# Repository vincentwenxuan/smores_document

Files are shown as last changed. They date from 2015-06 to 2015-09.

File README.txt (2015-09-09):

This file focus on the auto-calibration method. To make the codes work, we added and changed some commands in the main functions, both in atmega and stm32.
Some head files and c/cpp files also changed or added.

1. common_macros.h are added to store some macros which was defined in main functions. So pay attention about the multi-definition before merging.

2. TWI_slave.h is changed to prevent multi-definition.

3. Wiper_encoder.c is changed to make sure we can request the raw data without position/velocity calculation.

4. atm_cali.c and .h are added to do the auto calibraion in atmega part. You can just add one command in main code: cali_mode();   The atm_cali.c will do the rest part.

5. stm_cali.cpp and .h are added to do the the auto calibration in stm32 part. You can just add one command in main code: cali_cmd(left_wheel_motor, right_wheel_motor, right_pan_tilt_motor, left_pan_tilt_motor); The stm_cali.cpp will do the rest part.

6. USART.c and .h are deleted to prevent the memory overflow in atmega. Remember to put them back when new chips are applied.

7. smores_wiper_encoder_test is used to show the 4 calibrated values (adc0_0, adc0_180, adc1_0, adc1_180)

8. smores_wiper_encoder_calibration is the old version. (We found out the new version is not working at all. We cannot read the data from usb.)

9. We put all the things to the smores_autocali (atmega part) and smores_autocalibration (stm32 part).

10. We change the project_message_types.h, add the autocalibration command type

P.S. resolution calculation is wrong! (FIXED)

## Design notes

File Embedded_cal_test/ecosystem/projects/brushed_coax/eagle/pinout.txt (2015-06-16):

ZB_SCLK = SPI1_SCK
ZB_MISO = SPI1_MISO
ZB_MOSI = SPI1_MOSI
ZB_SEL  = SPI1_NSS
ZB_IRQ  = 13

IMU_INT = 43
IMU_SDA = I2C1_SDA, 46
IMU_SCL = I2C1_SCL, 45

VOLT_SENSE = 10
AMP_SENSE = 11

IN_1_HIGH = TIM1_1,  29
IN_1_LOW  = TIM1_1N, 26
IN_2_HIGH = TIM1_2,  30
IN_2_LOW  = TIM1_2N, 27

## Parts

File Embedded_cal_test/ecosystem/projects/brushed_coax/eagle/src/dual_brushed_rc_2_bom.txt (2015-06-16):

Partlist exported from /media/work/ecosystem/projects/brushed_coax/eagle/src/dual_brushed_rc_2.sch at 10/27/14 9:44 AM

Qty Value          Device                Package       Parts                                                  Description                                                                                  
4                  LEDCHIPLED_0603       CHIPLED_0603  BLUE_LED, GREEN_LED, RED_LED, YELLOW_LED               LED                                                                                          
1                  M02-JST-2-PTH-NO_SILK JST-2-PTH-NS  JP2                                                    Header 2                                                                                     
1   0896FB15A0100  0896FB15A0100         0896FB15A0100 BALUN1                                                                                                                                              
5   1 kΩ           R-US_R0402            R0402         R3, R4, R5, R6, R7                                     RESISTOR, American symbol                                                                    
6   1 µF           C-EUC0402             C0402         CB1, CB2, CB3, C_MC_VDDA_1, C_MC_VDD_2_1, C_MC_VDD_3_1 CAPACITOR, European symbol                                                                   
1   1.2 kΩ         R-US_R0402            R0402         R_CLK_VDIV1_1                                          RESISTOR, American symbol                                                                    
2   10 kΩ          R-US_R0402            R0402         I2C_PULLUP_1, I2C_PULLUP_2                             RESISTOR, American symbol                                                                    
2   10 nF          C-EUC0402             C0402         C6, VLOGIC_BYPASS_1                                    CAPACITOR, European symbol                                                                   
4   100 nF         C-EUC0402             C0402         C2, C3, C_IMU_B_1, C_IMU_FILT_1                        CAPACITOR, European symbol                                                                   
1   100 pF         C-EUC0402             C0402         C5                                                     CAPACITOR, European symbol                                                                   
1   2.2 nF         C-EUC0402             C0402         C_IMU_CP_1                                             CAPACITOR, European symbol                                                                   
1   2.2 µF         C-EUC0603             C0603         C1                                                     CAPACITOR, European symbol                                                                   
1   2.7 kΩ         R-US_R0402            R0402         R2                                                     RESISTOR, American symbol                                                                    
1   220 Ω          R-US_R0402            R0402         R_CLK_VDIV2_1                                          RESISTOR, American symbol                                                                    
1   3.3 µF         C-EUC0603             C0603         C_MC_VDD_1_1                                           CAPACITOR, European symbol                                                                   
3   33 kΩ          R-US_R0402            R0402         R9, R10, R_BOOT_PU_1                                   RESISTOR, American symbol                                                                    
1   47 µF          C-EUC0805             C0805         C4                                                     CAPACITOR, European symbol                                                                   
1   6.8 kΩ         R-US_R0402            R0402         R1                                                     RESISTOR, American symbol                                                                    
1   ASTX-H11       ASTX-H11              ASTX-H11      U$54                                                                                                                                                
1   AT86RF         AT86RF                QFNN32        U$51                                                                                                                                                
4   BAS 52-02V     DIODE-SOD523          SOD523        D1, D2, D3, D4                                         DIODE                                                                                        
1   DRV8850_RGY_24 DRV8850_RGY_24        RGY_24        U1                                                     The DRV8850 from Texas Instruments is a Low-Voltage H-bridge IC With LDO Voltage Regulation. 
1   MPU-6050       MPU-6050              QFN24         U$46                                                                                                                                                
4   PADSURF        PADSURF               PAD_1_SURF    U$55, U$58, U$59, U$60                                                                                                                              
1   SM06B-SRSS-TB  SM06B-SRSS-TB         SM06B-SRSS-TB U$56                                                                                                                                                
1   STM32F303CX    STM32F303CX           LQFP48        U$1                                                                                                                                                 
7   TPTP10SQ       TPTP10SQ              TP10SQ        TP1, TP2, TP3, TP4, TP5, TP6, TP7                      Test pad                                                                                     
1   Whip           PINHD-1X01_2.54       1X01          JP1                                                    PIN HEADER

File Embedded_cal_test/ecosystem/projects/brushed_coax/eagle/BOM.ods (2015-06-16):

Brushed Coax BOM
Item | Qty | Part | Qty 1 | Qty 100 |  | Cost 1 | Cost 100
Radio | 1 | AT86RF212 | 6.21 | 4.5468 |  | 6.21 | 4.5468
Balun | 1 | 0896FB15A0100E | 1.07 | 0.5738 |  | 1.07 | 0.5738
Clock | 1 | ASTX_H11 | 3.34 | 2.7232 |  | 3.34 | 2.7232
Motor Driver | 1 | DRV8850 | 1.69 | 1.1794 |  | 1.69 | 1.1794
IMU | 1 | MPU-6050 | 5.87 | 5.59 |  | 5.87 | 5.59
Controller | 1 | STM32F303CCT6 | 7.83 | 5.7942 |  | 7.83 | 5.7942
Bulk Cap | 1 | CL21A476MQCLRNC | 0.77 | 0.3575 |  | 0.77 | 0.3575
LED | 4 | Generic | 0.28 | 0.1188 |  | 1.12 | 0.4752
 |  |  |  |  | TOTAL | 27.9 | 21.2401

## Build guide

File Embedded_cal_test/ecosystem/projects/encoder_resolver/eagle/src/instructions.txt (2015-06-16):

Here they are,  good luck!  Remember to have good power supply filtering.  The 12V rail may be really noisy.  Transformer part# is in the documents.  Remember to hook it up correctly paying attention to the dots.  Side with the higher inductance in model has more windings.  If you pick another op-amp, can you show me which one?  I want to make sure it will pass checks for output current, high and low voltage under load, input bias current, offset, and PSRR.  Thanks.

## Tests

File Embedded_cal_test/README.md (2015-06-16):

Embedded
========
Embedded Software for SMORES, including STM32F303 part, ATmega88 part and Gumstix part.

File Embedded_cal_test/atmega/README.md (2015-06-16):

ATmega88
========
The folder contains the ATmega88 template, atmega programming environment, examples showing how to use the libraries and Utility.
 - ATmega88Template: The template contains all necessary files for user to work with ATmega88;
 - atmega: 
    * common_library: contain commonly used libraries for users, including common_peripherals, ADC, PWM, TWI_slave and USART;
    * project: all projects' folder are here and put all source files including main.c in src folder and put all header files in inc folder;
    * Makefile: common Makefile;
    * smores_common_library: contain commonly used libraries for smores project, including drive_coils and wiper_encoder.
 - Utility: all necessary files and README for programming atmega in Windows.

In order to use the programming environment, install gcc-avr, avr-libc, avrdude and libusb first.  

How to use:

 - Make your own project_peripherals_customized-name.h and modify project_peripherals.h accordingly;
 - Modify the Makefile in project to specify the user's onw directories for header files and source files.
 - Figure out what programmer you are using and change the PROGRAMMER in project Makefile accordingly;
 - All the codes are made to work with 8MHz internal RC oscillator. With a new ATmega88 chip, first program the fuse using “make fuse”;
 - Use command “make” to generate the object files and hex file and all object files are in obj folder;
 - Use command “make flash” to flash the code to the chip;

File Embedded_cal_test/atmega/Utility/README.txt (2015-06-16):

Use AVR-GCC and avrdude on Windows:

1. Install WinAVR on the computer;

2. Copy libusb0.dll from libusb-win32-bin-1.2.6.0/libusb-win32-bin-1.2.6.0/bin to Windows/Syswow64 if the OS is 64 bit or Windows/System32 if the OS is 32 bit;

3. Copy libusb0.sys to  Windows/System32/drivers/libusb0.sys;

4. Connect AVRISP mkII with your compute. When it asks whether you wish to install the drivers for it automatically or manually, choose MANUAL, and select libusb-win32-bin-1.2.6.0 folder or avrispmkii_libusb-win32_1.2.1.0 folder. If it’s detected successfully you should be able to see AVRISP mkII under Atmel USB Devices in Device Manager.

5. If it’s not successful detected when you plug in AVRISP mkII, check if the AVRISP mkII under Jungo Connectivity. Right click this and select “Update Driver Software”, then select “Browse my computer for driver software” and go to avrispmkii_libusb-win32_1.2.1.0 folder to install the driver.

6. Open cmd.exe and go to the project folder which contains the Makefile. 

7. Input “make” to make the .hex file, input “make fuse” to program the fuse and input “make flash“ to flash the code.

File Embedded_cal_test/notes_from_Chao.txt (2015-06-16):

All smores code is named smores_

ecosystem:
- all smores-specific library files are in smores_common
- already modify Makefile to compile codes in smores_common
- DC_Motor, Polynomial, Trajectory, PID_Control, Wheel_Control
- smores_template and stm32f303_discovery_template
- smores_pid_control is the previous version of pid controller which is useless now.

atmega:
- written outside ecosystem (all code in atmega directory)
- atmega template includes all coding part you need to program ATmega and it can be used independently, but it's not necessary for smores project
- Projects in project directory
- To set up new project, copy smores_face_board_template and rename
- twi = I2C testing
- wiper_encoder_test is the face board testings setup code
- the Utility folder allows you do use windows
- Don't use ATMEL studio in windows. Just use a normal text editor
- common library includes basic functions (ADC, PWM, etc)
- example includes the examples of USART, PWM, ADC and TWI

In the Makefile, there are four commands:
 - make, make flash, make clean, make fuse
 - with the new atmega chip, you must program the fuse first (when you first start using the chip)
    - you can't program the chip correctly with make flash before doing this.
    - it configures the clock.

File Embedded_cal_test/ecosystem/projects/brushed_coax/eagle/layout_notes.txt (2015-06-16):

************************************************************************
Orginal Layout Notes:

--Add large supply cap to motor driver sheet.
--Eliminate capacitors to balun balanced inputs and add 100 p capacitor to balun unbalanced output, as per reference design from Atmel.

************************************************************************
After Testing:

Fix:

OK -- flip crystal footprint (upside-down)
OK -- feed motor controller / LDO enable direct from battery
OK -- protect gound pad on bottom of motor driver
-- add vias to SPI lines
-- add vias to I2C lines
-- add vias to clock lines

MAV Features:

OK -- shrink board size
-- reduce board thickness
NO -- consider 45 degree IC orientations
OK -- check on 0402 footprint sizes
OK -- add more LEDs (red, yellow, green, blue, white)
OK -- swap motor thru holes for pads
OK -- plan for battery connector
OK -- add analog / uart pins for sonar sensor
OK -- add pwm pads to control CX2

Dongle Features:

-- design as single-sided two-layer
-- add silkscreen labels for output pads on both sides
-- add vias near output pads on both sides
-- charge state indicator (or on MAV?)
-- power indicator

-- Power features
  -- MAV battery removable
  -- MAV battery easily disconnected (power switch)

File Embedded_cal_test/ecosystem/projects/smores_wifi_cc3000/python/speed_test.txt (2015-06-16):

Summary created by Wireshark  (v1.10.6 from master-1.10)

File: 
   Name:             /tmp/wireshark_pcapng_wlan0_20150603181214_NTTekb
   Length:            754000798 bytes
   Format:            Wireshark/... - pcapng
   Encapsulation:    Ethernet

Time:
   First packet:    First packet:   
   Last packet:    Last packet:    
   Elapsed:    Elapsed: et:    Last packet: ast 

Capture:
   OS: Linux 3.11.0-12-generic
   Capture application: Dumpcap 1.10.6 (v1.10.6 from master-1.10)

   wlan0:
      Dropped packets: 5294 (0.056%)
      Capture filter: none
      Link type: Ethernet
      Packet size limit 65535 bytes

Statistics:
   Packets: 9423845
   Between first and last packet:100.520 sec
   Avg. packets/sec: 93750.822
   Avg packet size: 45.019 bytes
   Bytes: 424255984
   Avg bytes/sec: 4220607.109
   Avg Mbit/sec: 33.765

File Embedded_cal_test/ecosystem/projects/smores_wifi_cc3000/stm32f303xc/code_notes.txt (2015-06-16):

Change Magnet state number to the actual i2c address macros (fix this in python) 

Get rid of all these flags 

switch to my wifi sending method use datamanger to access stored structs

More handling functions with following workflow 
pass the dataManager class/struct to all of them 
 velocity Handler 
    '->right_DOF handler 
	deal with flagging for velocity or torque 
	'->dof_cmd_handler 

  torque handler 
   '-> right_DOF handler 
	deal with flagging for velocityor torque 
	'-> dof_cmd_handler 

Read Faces funciton 
'> request_face_state x4  
 	'-> write face_state to struct
		(put vel and pos estimations in here) 

init_wheel_pos (whatever wheel ) 
   '-> set_face_state 

global changing variables / flags can be in device manager 

Setting the face names to be the same number as i2c address 

current_position_right why can't we retrieve from the object? in the callbacks

Need to fix classes So that updateState explain the debug shit but i guess its ok ? 

check header symbol defs

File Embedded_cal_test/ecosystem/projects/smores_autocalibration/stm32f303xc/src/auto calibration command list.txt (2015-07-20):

The target face will rotate after the command is received, EXCEPT for tilt command.
For left, right, pan calibraion, you just need to send the command and wait.
For tilt calibration, three different commands need to be sended. And you need move the face manually.

left face auto calibraion: 50
right face auto calibration: 51
pan auto calibration: 52
tilt calibration at -90 degree: 53
tilt calibration at 0 degree: 54
tilt calibration at 90 degree: 55

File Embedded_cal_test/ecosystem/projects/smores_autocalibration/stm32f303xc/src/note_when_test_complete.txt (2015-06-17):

motor init part should be put back(currently commented)

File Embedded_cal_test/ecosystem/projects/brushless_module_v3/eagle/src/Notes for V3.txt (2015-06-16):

Round, not square
Mount holes not 90deg from usb (for mounting reasons) (mounting holes at 45deg, usb and motor at ordinal)
Radio footprint vs atmel gerbers
Can the Vreg tell us when it's on?  Yes, use the PG pin!  Use micro internal pu. (Don't bother, see below)
Yash sexy button (vreg with enables required)
Bigger antenna via (or chip antenna)
Current sensor voltage divider needs 1ks, not 10ks or 1.65 ref voltage (probs 1.65 ref reg) (dac?)
Should have individual voltage dividers because long wires crossing fets get noise
Route analog lines from current sensors smartly, no crossing fets or poss differential measurement
move current sensors and thermistor up so 3.3 doesn't have to go to bottom
Big ceramic vs tant?
smaller fets?
smd usb (DONE)
cap on reset?
Thermistor? If board could be smaller, no

Vreg takes up a lot of space!  Can we make it smaller???
TPS62172DSGT with BRC2012T2R2MD .5A more efficient and inductor smidge smaller
TPS62162DSGT with SRP2010-2R2M 1A

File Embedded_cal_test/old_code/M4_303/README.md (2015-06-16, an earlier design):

M4_303
========
Use Utilities/zadig to install the drivers for the F303. For more details see getting started with M4 on the medesign website.

Use the M4_303/M4303_template to get started.
The HSE clock settings have been updated for 16Mhz input clock. Hence the template will no longer work with the discovery board. Either use the discovery template or copy the correct clock settings from Useful_libraries/Disco_clock_config
mGeneral has led settings for the SMORES board. change them according to custom board

For M4_303 library [apis](#)

USB not tested yet.
Memory usage shown needs to be updated for the f303 in the makefile

There are example codes and user libraries in the M4_303/user_libraries_projects
each library has its own platform config. You can combine them into one.

NOTE - it is recommended not to toggle the leds on the smores board faster than 2 MHz

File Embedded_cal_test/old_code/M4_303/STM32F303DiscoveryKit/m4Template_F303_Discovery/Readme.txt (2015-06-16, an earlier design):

This template is for STM32F3DiscoveryKit. It has 8 on-board LEDs and 1 user buttons. With this code, LED4, LED5, LED8 and LED9 are on, and LED6 and LED7 are off, and LED10 is toggling. Push the user button to turn off LED3.

Connect BOOT0 with 3V and Press RESET button before you flash the code. 
Disconnect BOOT0 with 3V and Press RESET button again to run the code.

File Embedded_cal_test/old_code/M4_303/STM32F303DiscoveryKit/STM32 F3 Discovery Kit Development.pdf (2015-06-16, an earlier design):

## ST-‐Link

Preparation:

1. If you haven't installed homebrew:
ruby -‐e "$(curl -‐fsSL https://raw.github.com/mxcl/homebrew/go)"
2. brew tap nitsky/stm32
3. Install the compiler
brew install arm-‐none-‐eabi-‐gcc
brew install -‐-‐HEAD stlink

For Mac:

For Linux, it should be very similar.

1. Download stm32_F3_Discovery_template
2. Connect the board with your computer
Go to the directory of your code, and open a terminal, run: make. There should be a folder named build.

3.

4. open another terminal, run: st-‐util
5. open another terminal, go into build folder, run: arm-‐none-‐eabi-‐gdb
6. In GDB,
(gdb) tar ext :4242
(gdb) load program.elf
(gdb) run

Flash the Code:

Download m4Template_F303_Discovery and follow the instructions in Readme.txt.

## USB

# STM32 F3 Discovery Kit Development

Tuesday, May 6, 2014 2:20 PM

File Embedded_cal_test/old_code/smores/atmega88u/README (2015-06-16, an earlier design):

need to add a custom make file / add files

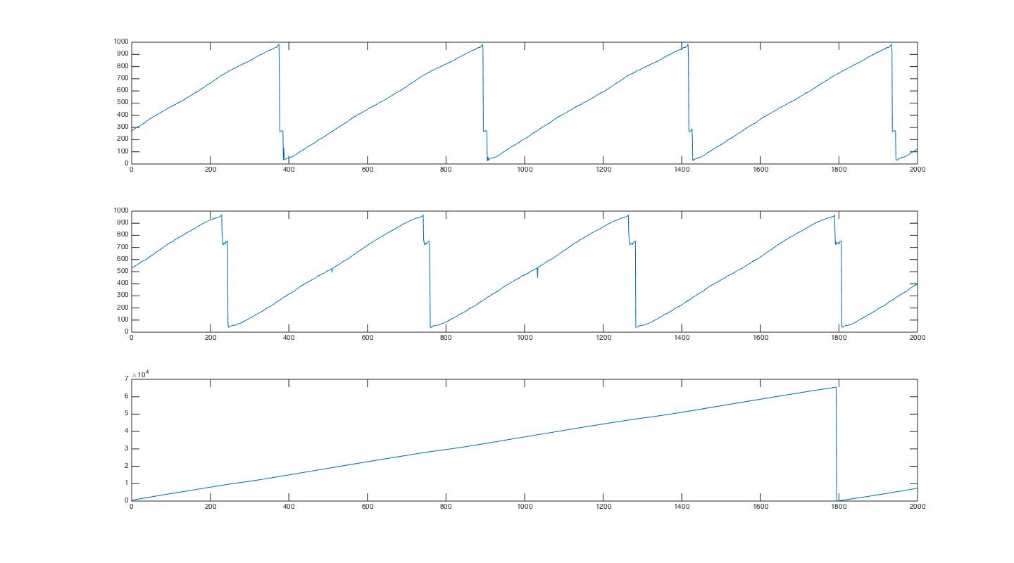
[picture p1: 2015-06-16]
Embedded_cal_test/ecosystem/projects/smores_wiper_encoder_stm32f303_discovery/matlab/data_set_10.jpg

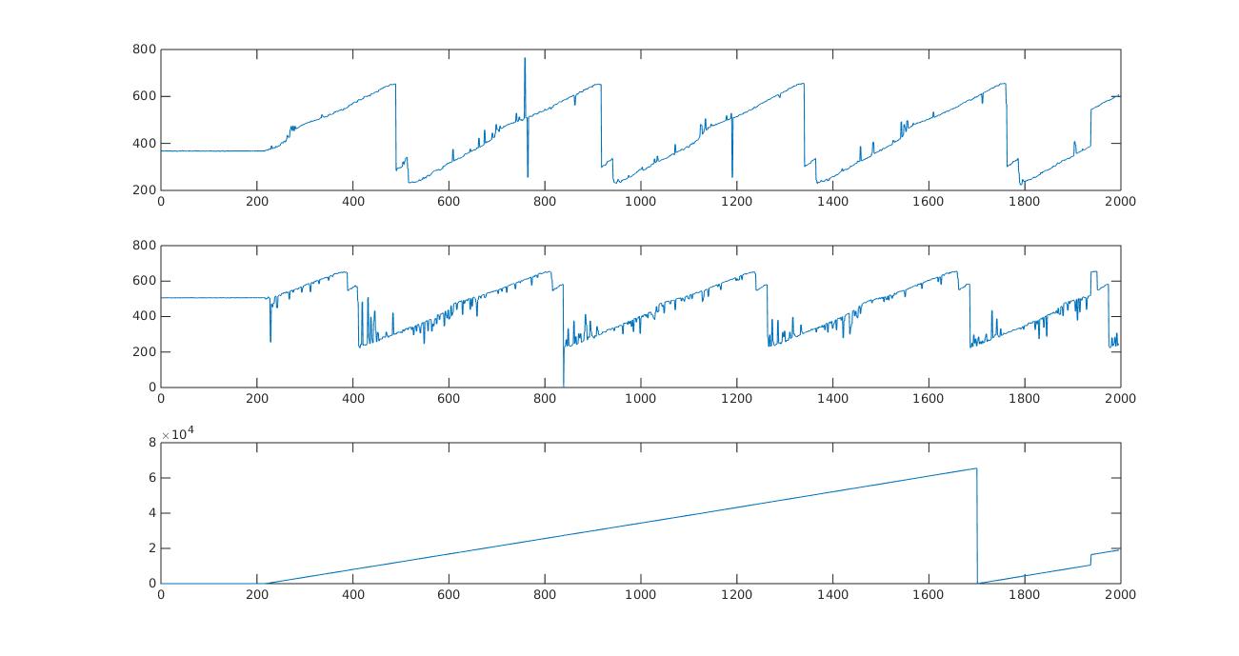
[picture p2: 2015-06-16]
Embedded_cal_test/ecosystem/projects/smores_wiper_encoder/matlab/data_set_7.jpg

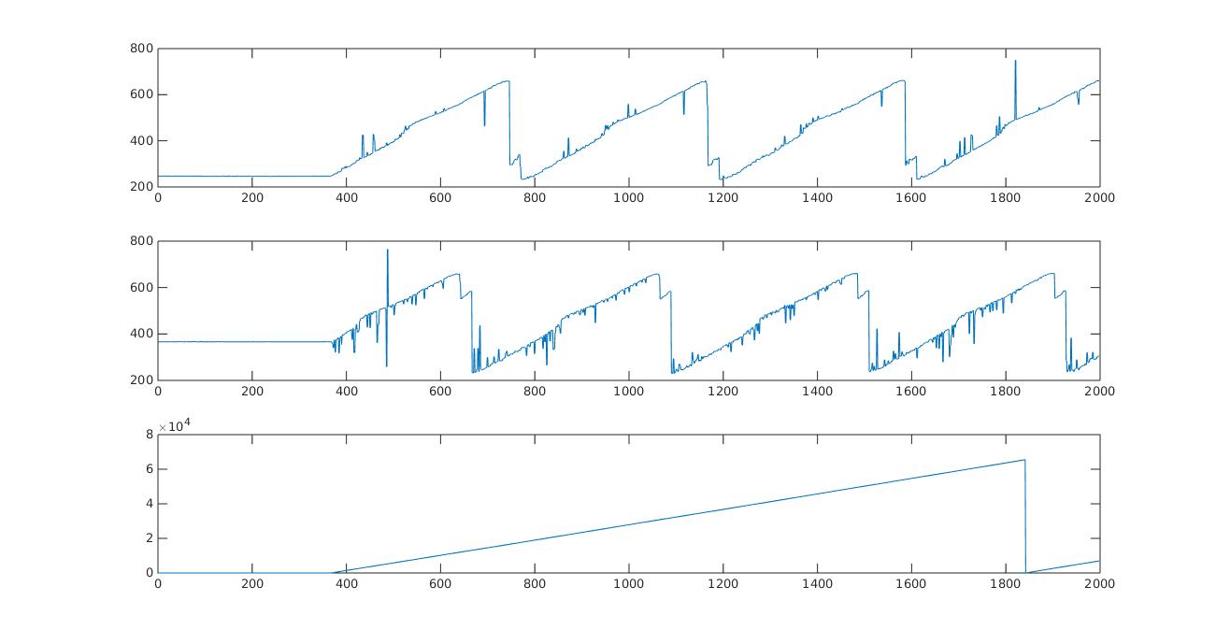
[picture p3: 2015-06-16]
Embedded_cal_test/ecosystem/projects/smores_wiper_encoder_stm32f303_discovery/matlab/data_set_8.jpg

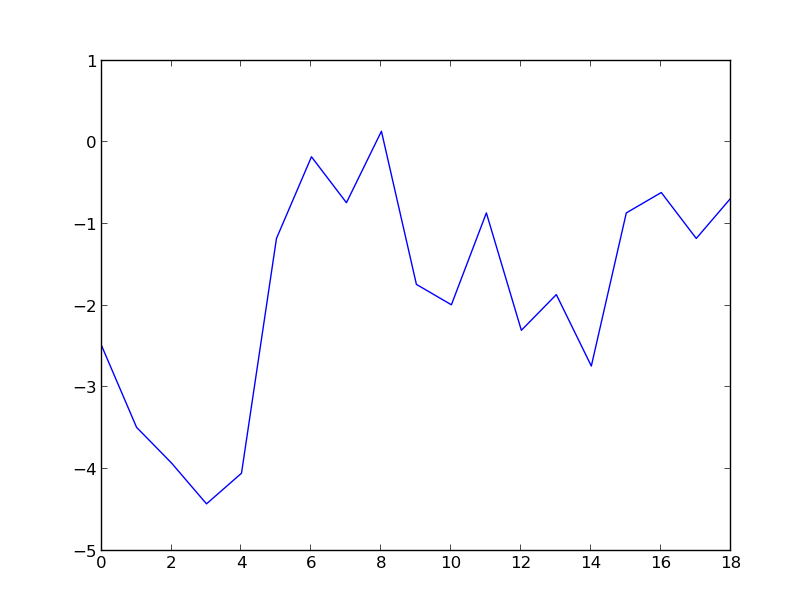
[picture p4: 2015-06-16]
Embedded_cal_test/ecosystem/projects/MPL311/py/src/ReadingPressureWithFan.png

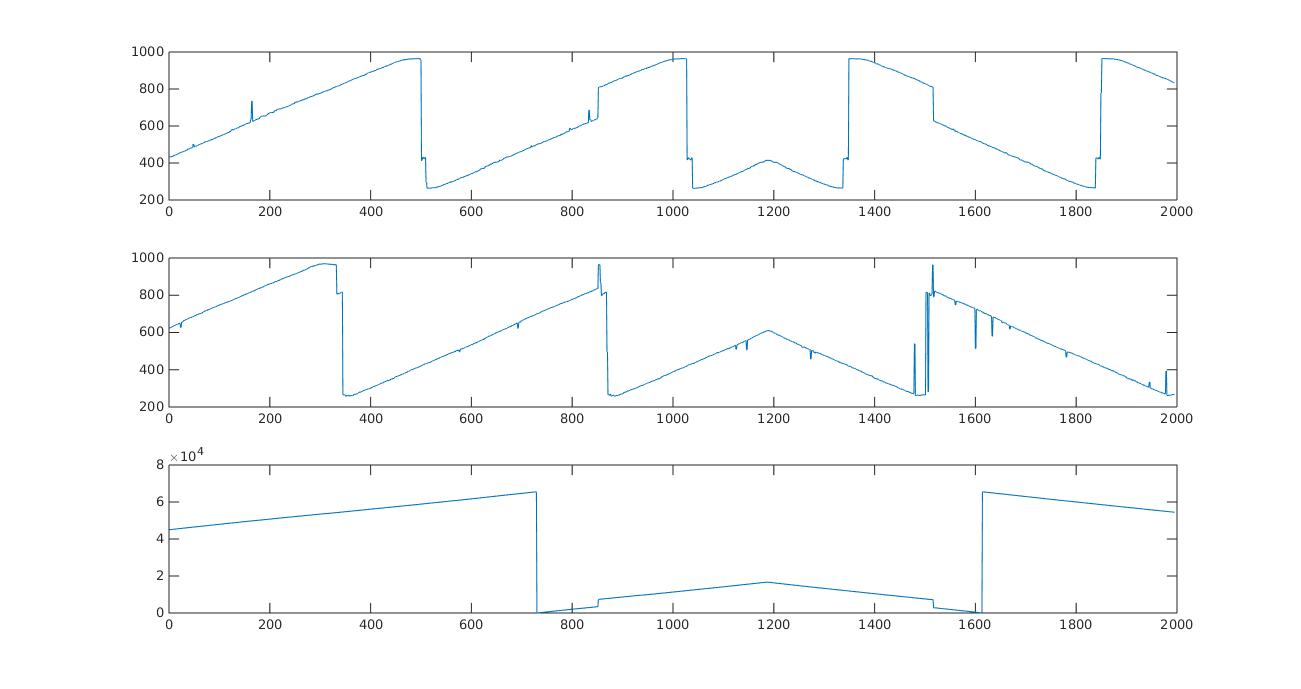
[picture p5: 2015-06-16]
Embedded_cal_test/ecosystem/projects/smores_wiper_encoder/matlab/data_set_9.jpg

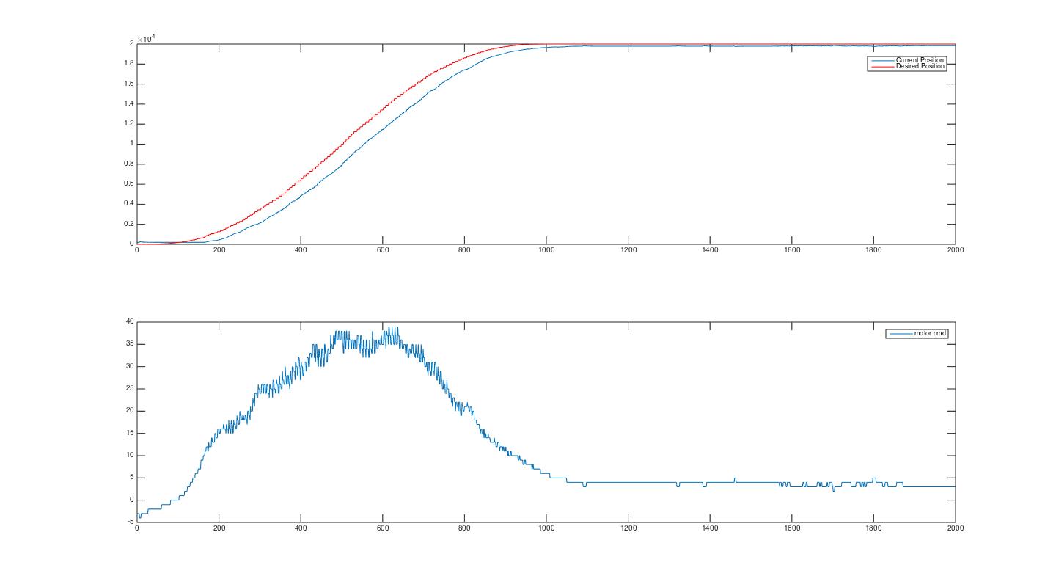
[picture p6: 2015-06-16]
Embedded_cal_test/ecosystem/projects/smores_autocalibration/matlab/trajectory_position.jpg

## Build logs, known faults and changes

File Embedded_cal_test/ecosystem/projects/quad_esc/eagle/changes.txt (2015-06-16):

V1 > V2
1. Slave select pin of the ATRF needs to be connected to a microcontroller pin (any GPIO is fine).
2. Reset and Sleep pins of the ATRF need to be pulled up and down respectively. The reset pin can also be connected to a microcontroller pin if possible, though this is not really needed.
3. The pull-up resistors on the I2C need to be smaller, I see very slow rise times on the bus with the 10k ones. 1k works fine it seems, though I'm still not sure why we need such a strong pull-up.
4. Just check the RC timeout on the reset latch. One of the boards has an irritatingly short timeout.
5. Pull down on the gates of the motor FETs. ??Necessary??
6. Boot button change to button push hold plus power cycle with switch
7. Flyback diodes across motors
8. Test pads on comms lines (and perhaps others?)
9. Reverse polarity protection
10. IMU axis
11. Serial breakout?
12. EMI supression on USB

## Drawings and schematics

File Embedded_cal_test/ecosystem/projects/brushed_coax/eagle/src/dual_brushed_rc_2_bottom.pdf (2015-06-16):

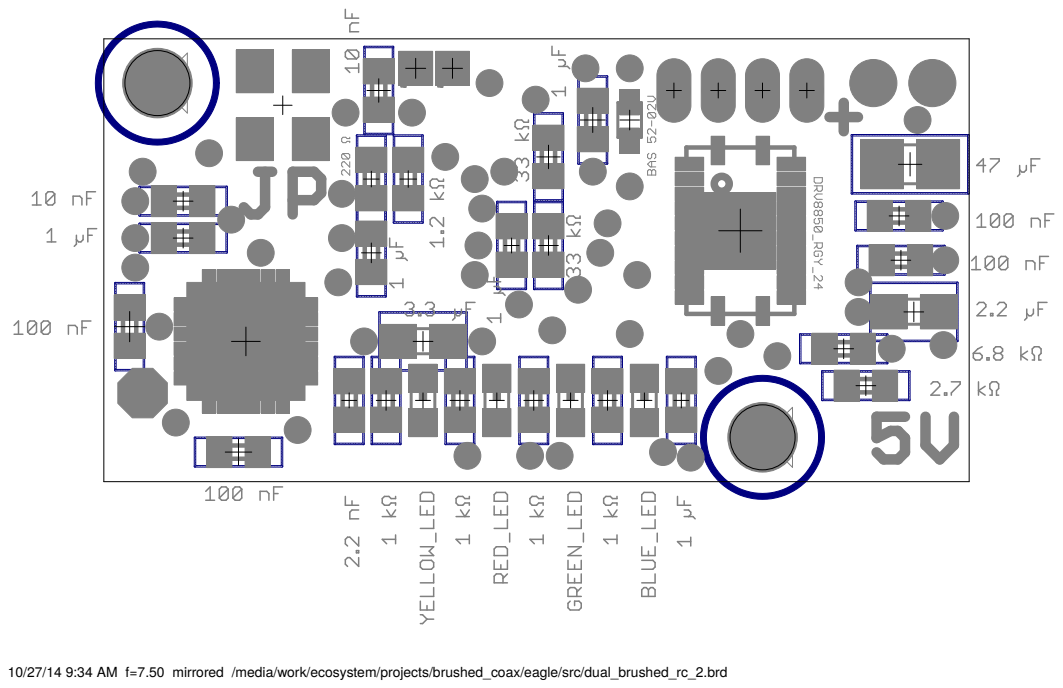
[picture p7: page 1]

10/27/14 9:34 AM f=7.50 mirrored /media/work/ecosystem/projects/brushed_coax/eagle/src/dual_brushed_rc_2.brd

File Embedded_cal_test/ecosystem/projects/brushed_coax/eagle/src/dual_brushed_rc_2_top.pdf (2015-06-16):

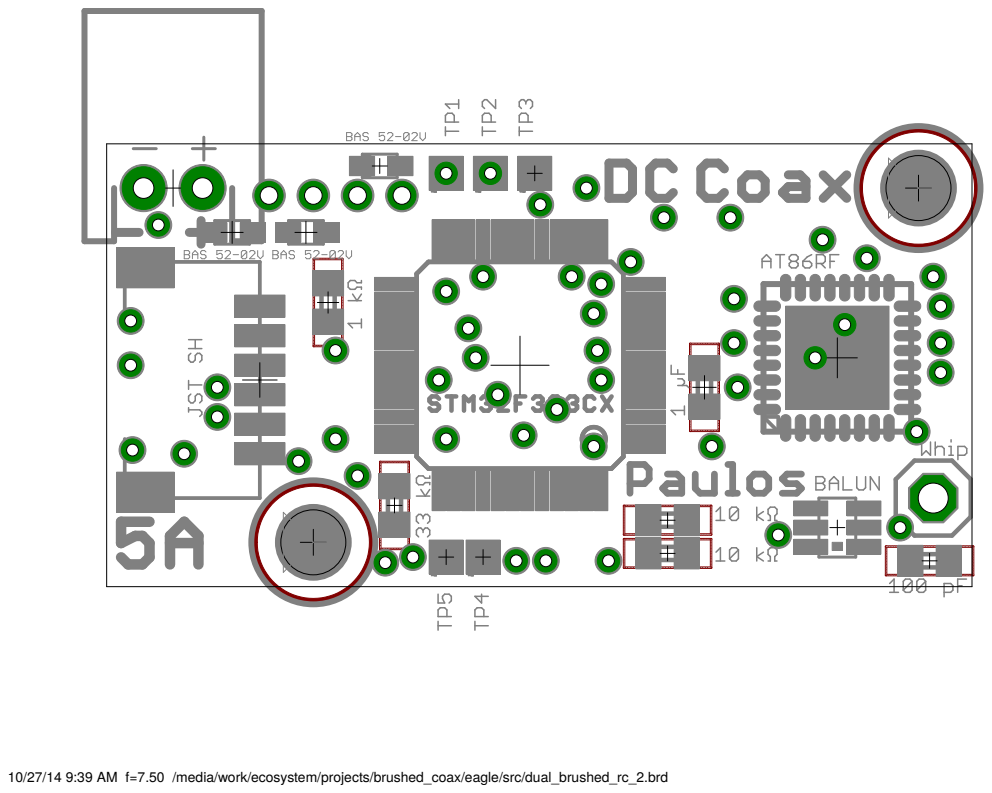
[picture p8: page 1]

10/27/14 9:39 AM f=7.50 /media/work/ecosystem/projects/brushed_coax/eagle/src/dual_brushed_rc_2.brd

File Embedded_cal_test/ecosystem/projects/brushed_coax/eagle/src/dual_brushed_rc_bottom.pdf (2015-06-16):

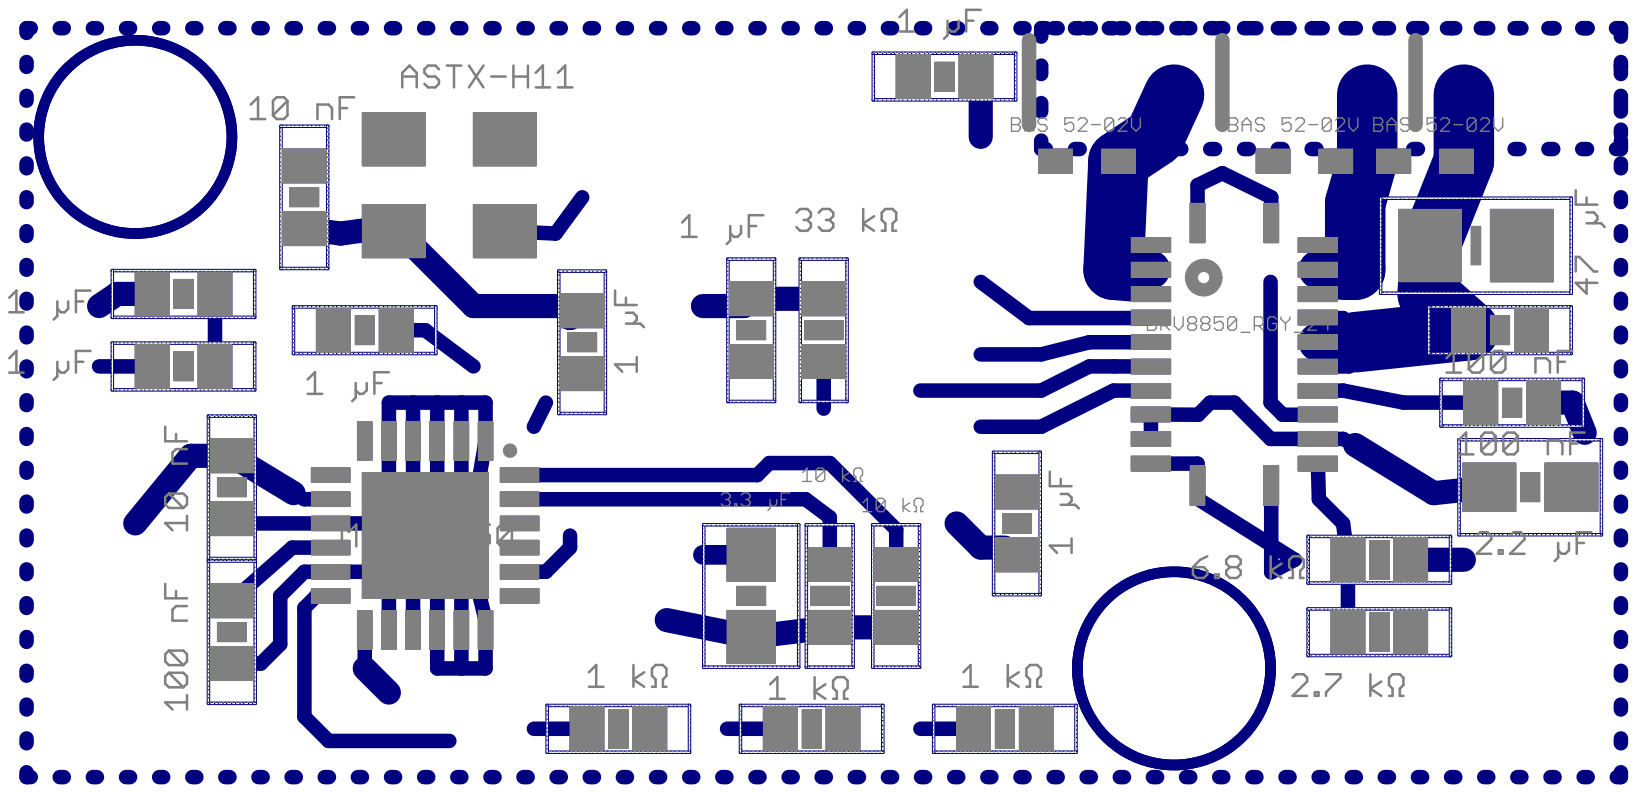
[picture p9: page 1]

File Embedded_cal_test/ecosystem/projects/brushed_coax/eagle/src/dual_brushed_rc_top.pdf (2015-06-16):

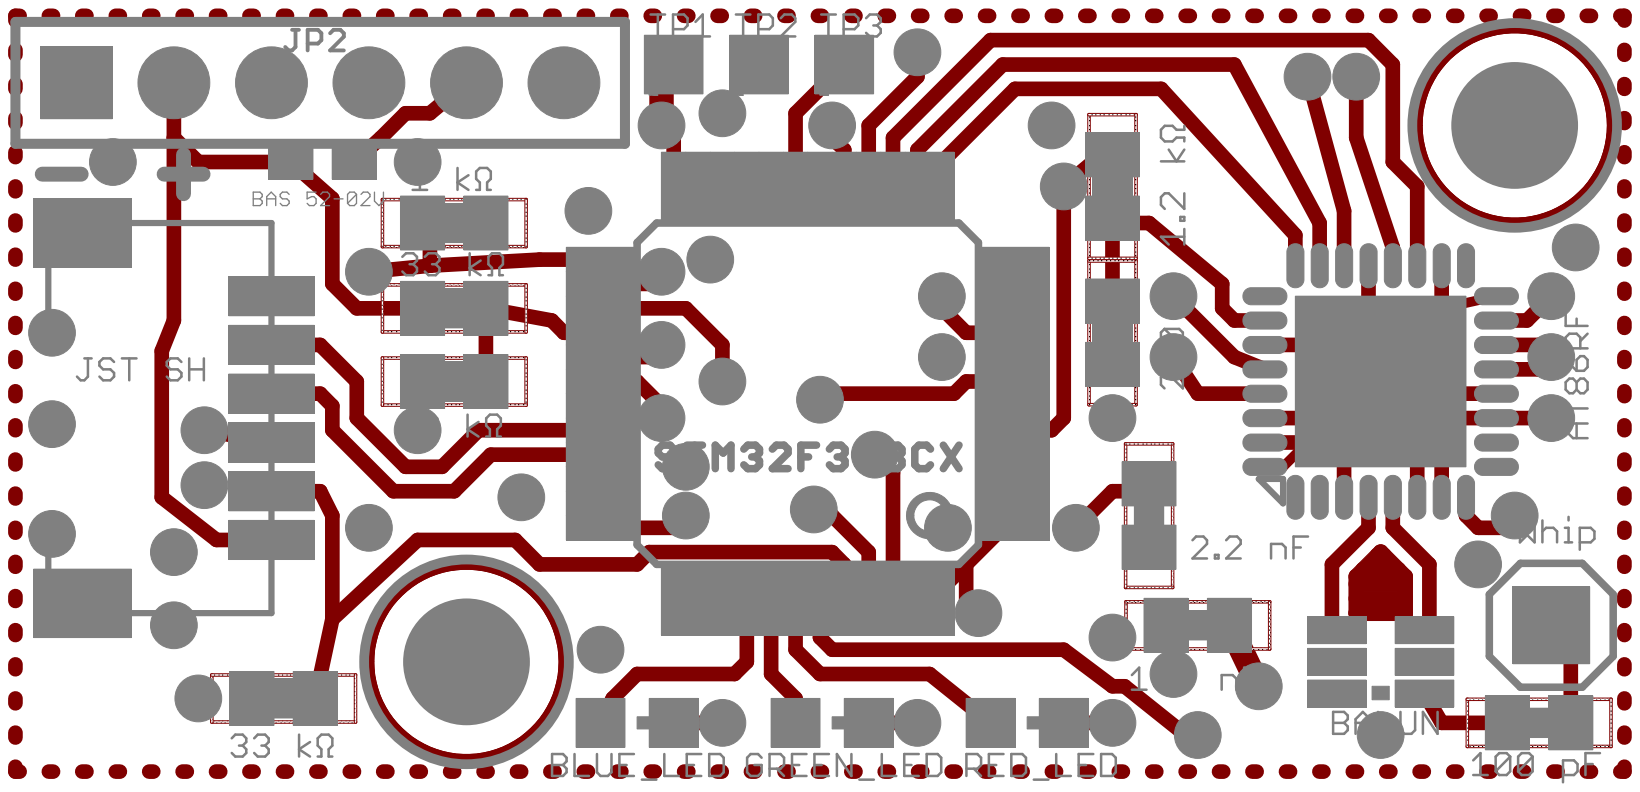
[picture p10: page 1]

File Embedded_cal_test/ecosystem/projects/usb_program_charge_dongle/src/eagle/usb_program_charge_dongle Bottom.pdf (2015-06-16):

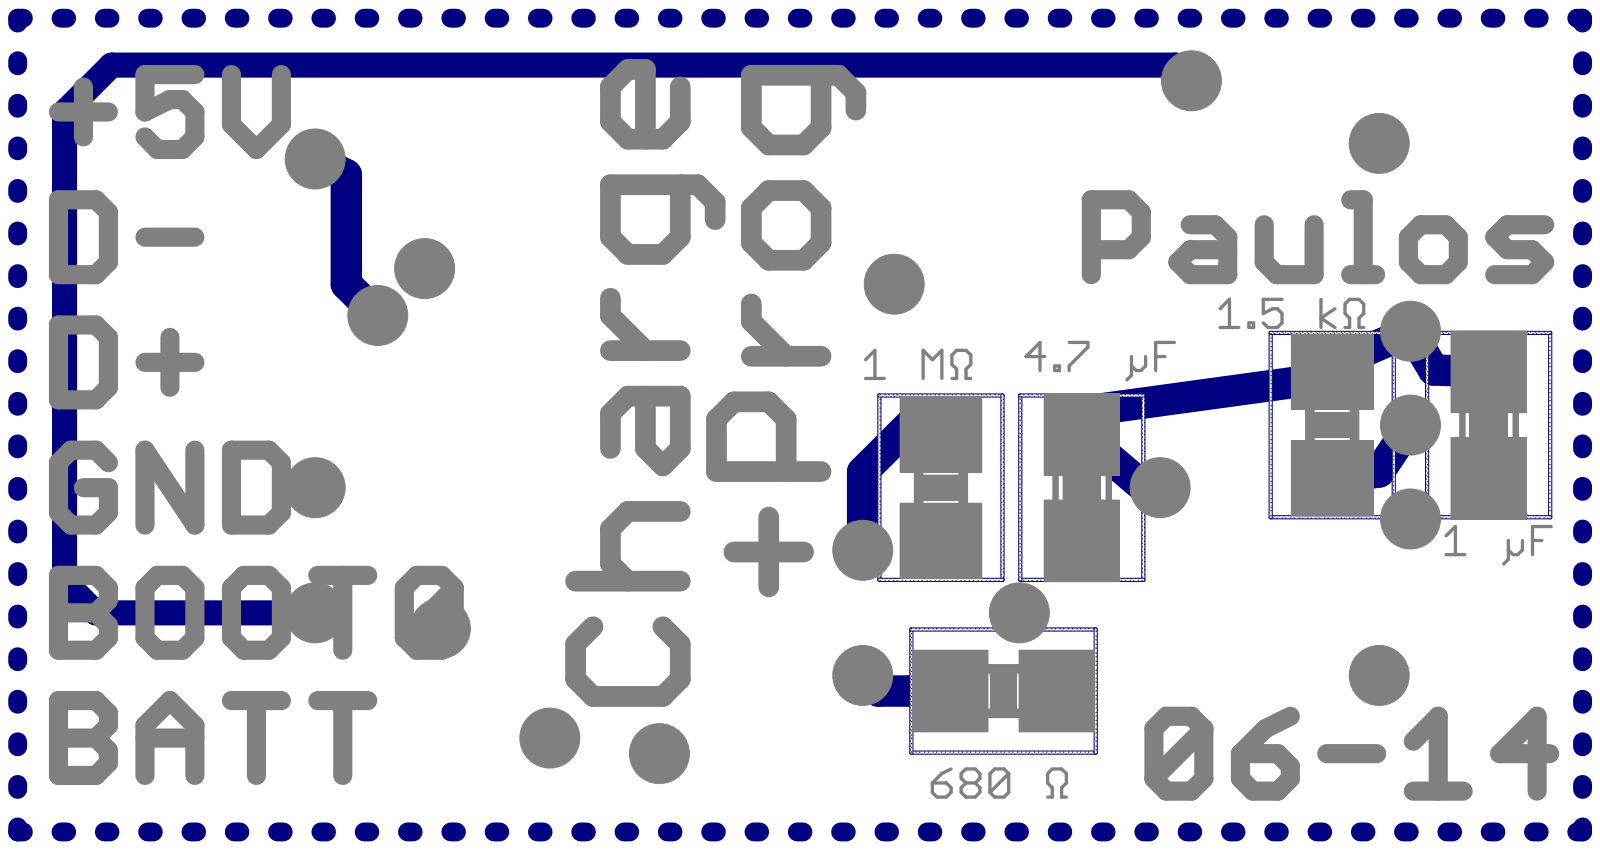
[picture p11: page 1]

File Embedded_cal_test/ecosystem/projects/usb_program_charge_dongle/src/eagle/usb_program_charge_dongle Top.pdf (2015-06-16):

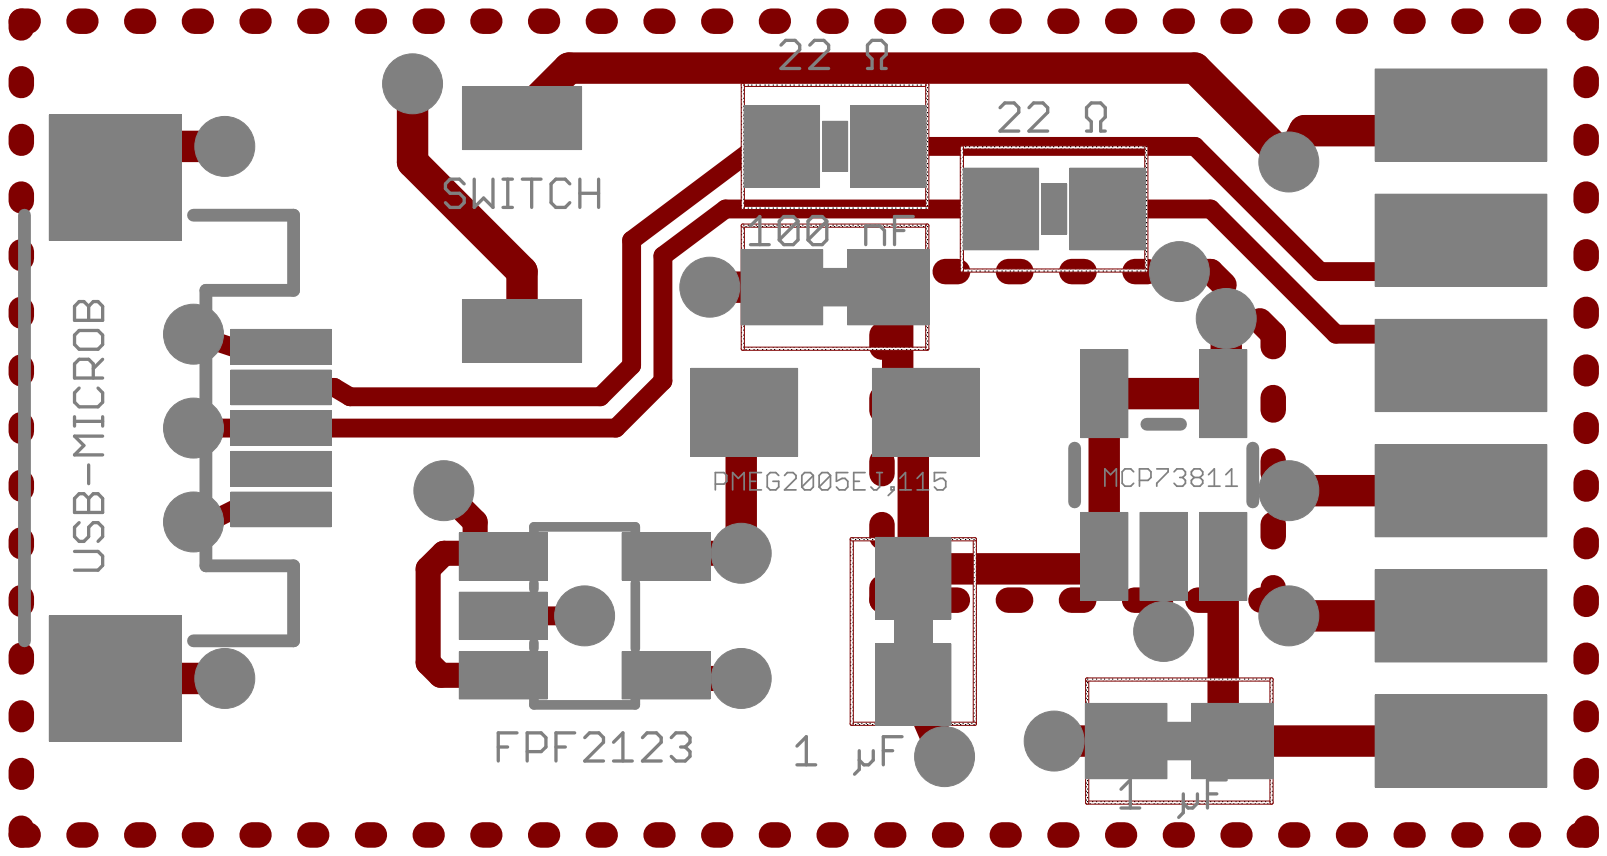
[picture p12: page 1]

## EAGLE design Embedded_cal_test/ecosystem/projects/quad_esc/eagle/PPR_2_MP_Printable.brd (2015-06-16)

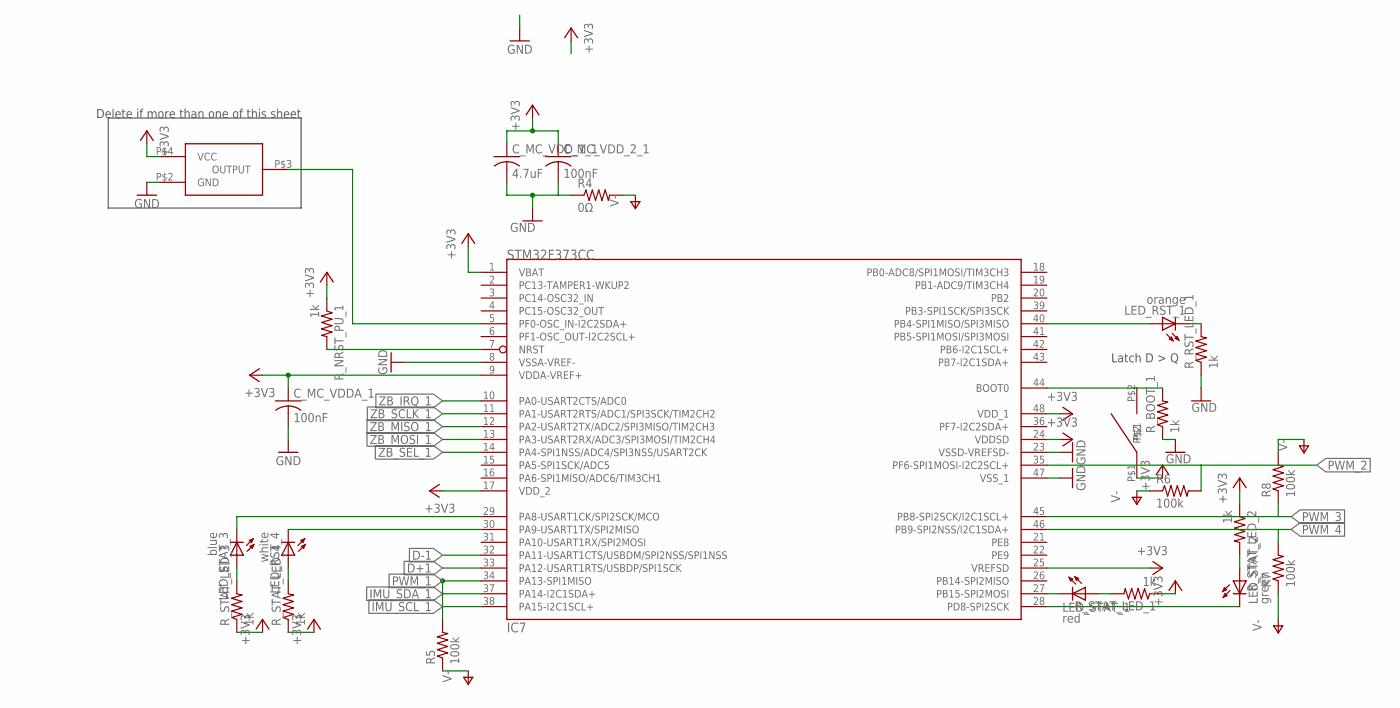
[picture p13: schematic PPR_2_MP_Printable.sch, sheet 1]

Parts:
C_MC_VDDA_1: 100nF; C0603
C_MC_VDD_1_1: 4.7uF; C0603
C_MC_VDD_2_1: 100nF; C0603
IC7: STM32F373CC; LQFP48
LED_RST_1: orange; CHIPLED_0603
LED_RST_4: white; CHIPLED_0603
LED_STAT_1: red; CHIPLED_0603
LED_STAT_2: green; CHIPLED_0603
LED_STAT_3: blue; CHIPLED_0603
OSC1: FOX924B; 4-SMD_5X3.2
R4: 0Ω; R0603
R5, R6, R7, R8: 100k; R0603
R_BOOT_1: 1k; R0603
R_NRST_PU_1: 1k; R0603
R_RST_LED_1: 1k; R0603
R_STAT_LED_1, R_STAT_LED_2, R_STAT_LED_3, R_STAT_LED_4: 1k; R0603
SW1: B3U

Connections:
16MHZ_3V3: IC7.5 (PF0-OSC_IN-I2C2SDA+), OSC1.P$3 (OUTPUT); also elsewhere on the board
+3V3: C_MC_VDDA_1.1, C_MC_VDD_1_1.1, C_MC_VDD_2_1.1, IC7.1 (VBAT), IC7.9 (VDDA-VREF+), IC7.17 (VDD_2), IC7.24 (VDDSD), IC7.25 (VREFSD), IC7.48 (VDD_1), OSC1.P$4 (VCC), R_NRST_PU_1.1, R_STAT_LED_1.1, R_STAT_LED_2.1, R_STAT_LED_3.1, R_STAT_LED_4.1, SW1.P$1; also elsewhere on the board
BOOT0_1: IC7.44 (BOOT0), R_BOOT_1.2, SW1.P$2
D+1: IC7.33 (PA12-USART1RTS/USBDP/SPI1SCK); also elsewhere on the board
D-1: IC7.32 (PA11-USART1CTS/USBDM/SPI2NSS/SPI1NSS); also elsewhere on the board
GND: C_MC_VDDA_1.2, C_MC_VDD_1_1.2, C_MC_VDD_2_1.2, IC7.8 (VSSA-VREF-), IC7.23 (VSSD-VREFSD-), IC7.47 (VSS_1), OSC1.P$2 (GND), R4.1, R_BOOT_1.1, R_RST_LED_1.1; also elsewhere on the board
IMU_SCL_1: IC7.38 (PA15-I2C1SCL+); also elsewhere on the board
IMU_SDA_1: IC7.37 (PA14-I2C1SDA+); also elsewhere on the board
LED_RST_1_1: IC7.40 (PB4-SPI1MISO/SPI3MISO), LED_RST_1.A
LED_RST_2_1: LED_RST_1.C, R_RST_LED_1.2
unnamed: IC7.27 (PB15-SPI2MOSI), LED_STAT_1.C
unnamed: LED_STAT_1.A, R_STAT_LED_1.2
unnamed: LED_STAT_2.A, R_STAT_LED_2.2
unnamed: IC7.28 (PD8-SPI2SCK), LED_STAT_2.C
unnamed: LED_STAT_3.A, R_STAT_LED_3.2
unnamed: LED_RST_4.A, R_STAT_LED_4.2
unnamed: IC7.30 (PA9-USART1TX/SPI2MISO), LED_RST_4.C
unnamed: IC7.29 (PA8-USART1CK/SPI2SCK/MCO), LED_STAT_3.C
NRST_1: IC7.7 (NRST), R_NRST_PU_1.2
PWM_1: IC7.34 (PA13-SPI1MISO), R5.2; also elsewhere on the board
PWM_2: IC7.35 (PF6-SPI1MOSI-I2C2SCL+), R6.2; also elsewhere on the board
PWM_3: IC7.45 (PB8-SPI2SCK/I2C1SCL+), R8.1; also elsewhere on the board
PWM_4: IC7.46 (PB9-SPI2NSS/I2C1SDA+), R7.2; also elsewhere on the board
V-: R4.2, R5.1, R6.1, R7.1, R8.2; also elsewhere on the board
ZB_IRQ_1: IC7.10 (PA0-USART2CTS/ADC0); also elsewhere on the board
ZB_MISO_1: IC7.12 (PA2-USART2TX/ADC2/SPI3MISO/TIM2CH3); also elsewhere on the board
ZB_MOSI_1: IC7.13 (PA3-USART2RX/ADC3/SPI3MOSI/TIM2CH4); also elsewhere on the board
ZB_SCLK_1: IC7.11 (PA1-USART2RTS/ADC1/SPI3SCK/TIM2CH2); also elsewhere on the board
ZB_SEL_1: IC7.14 (PA4-SPI1NSS/ADC4/SPI3NSS/USART2CK); also elsewhere on the board

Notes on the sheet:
Latch D > Q
Delete if more than one of this sheet

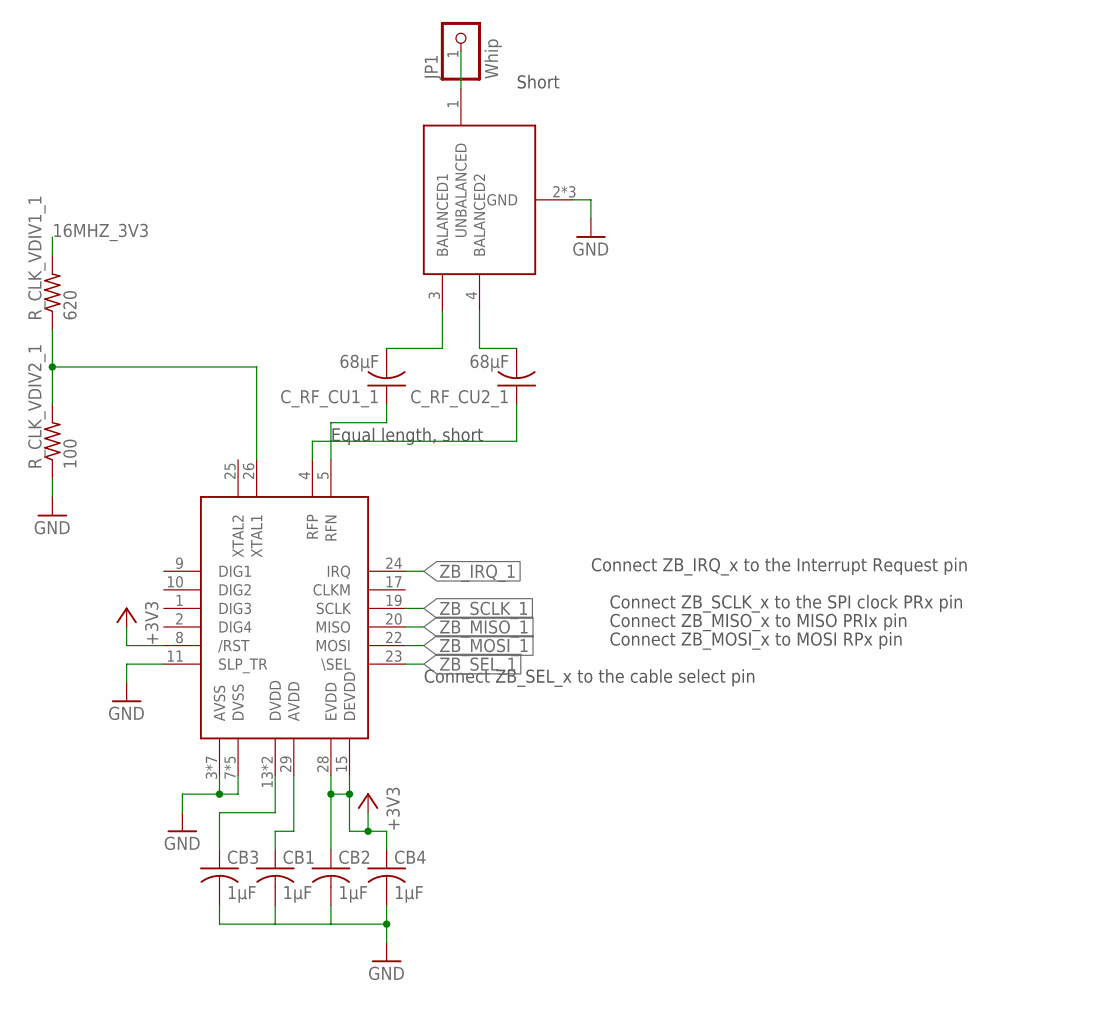
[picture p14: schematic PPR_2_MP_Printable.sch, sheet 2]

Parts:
BALUN1: 0896FB15A0100
CB1, CB2, CB3, CB4: 1µF; C0603
C_RF_CU1_1, C_RF_CU2_1: 68µF; C0603
JP1: Whip; 1X01M
RADIO1: AT86RF; QFNN32
R_CLK_VDIV1_1: 620; R0603
R_CLK_VDIV2_1: 100; R0603

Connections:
16MHZ_0V5_AC1: RADIO1.26 (XTAL1), R_CLK_VDIV1_1.1, R_CLK_VDIV2_1.2
16MHZ_3V3: R_CLK_VDIV1_1.2; also elsewhere on the board
+3V3: CB2.1, CB4.1, RADIO1.8 (/RST), RADIO1.15 (DEVDD), RADIO1.28 (EVDD); also elsewhere on the board
ANT1: BALUN1.1 (UNBALANCED), JP1.1
GND: BALUN1.2 (GND), BALUN1.5 (GND), BALUN1.6 (GND), CB1.2, CB2.2, CB3.2, CB4.2, RADIO1.3 (AVSS), RADIO1.6 (AVSS), RADIO1.7 (DVSS), RADIO1.11 (SLP_TR), RADIO1.12 (DVSS), RADIO1.16 (DVSS), RADIO1.18 (DVSS), RADIO1.21 (DVSS), RADIO1.27 (AVSS), RADIO1.30 (AVSS), RADIO1.31 (AVSS), RADIO1.32 (AVSS), RADIO1.EXP (AVSS), R_CLK_VDIV2_1.1; also elsewhere on the board
ZB_AVDD1: CB1.1, RADIO1.29 (AVDD)
ZB_BAL1_1: BALUN1.3 (BALANCED1), C_RF_CU1_1.2
ZB_BAL2_1: BALUN1.4 (BALANCED2), C_RF_CU2_1.2
ZB_DVDD1: CB3.1, RADIO1.13 (DVDD), RADIO1.14 (DVDD)
ZB_IRQ_1: RADIO1.24 (IRQ); also elsewhere on the board
ZB_MISO_1: RADIO1.20 (MISO); also elsewhere on the board
ZB_MOSI_1: RADIO1.22 (MOSI); also elsewhere on the board
ZB_RFN1: C_RF_CU2_1.1, RADIO1.4 (RFP)
ZB_RFP1: C_RF_CU1_1.1, RADIO1.5 (RFN)
ZB_SCLK_1: RADIO1.19 (SCLK); also elsewhere on the board
ZB_SEL_1: RADIO1.23 (\SEL); also elsewhere on the board

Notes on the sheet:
Connect ZB_SEL_x to the cable select pin
Connect ZB_MOSI_x to MOSI RPx pin
Connect ZB_SCLK_x to the SPI clock PRx pin
Connect ZB_MISO_x to MISO PRIx pin
Connect ZB_IRQ_x to the Interrupt Request pin
Equal length, short
Short

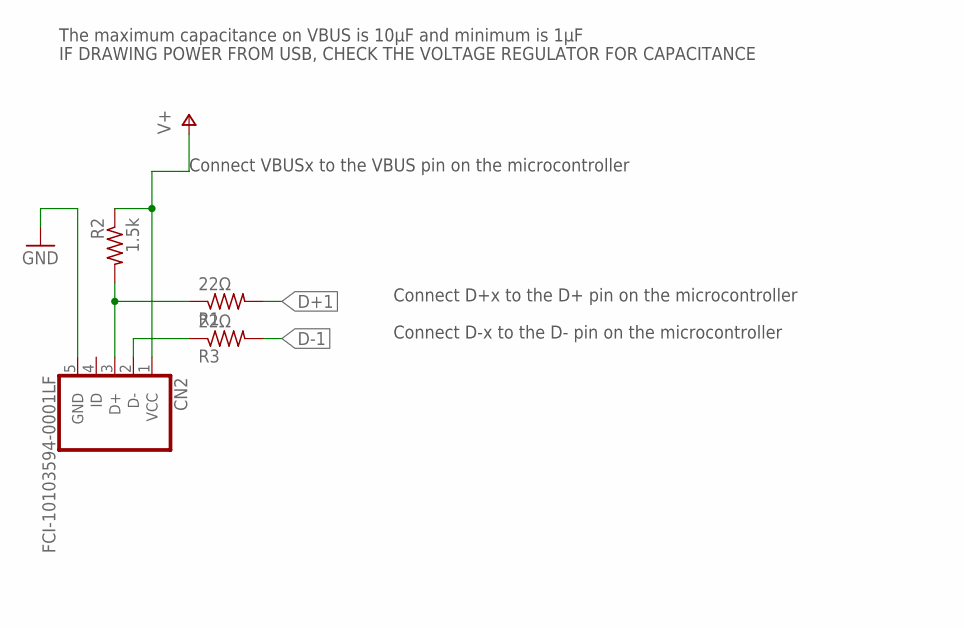
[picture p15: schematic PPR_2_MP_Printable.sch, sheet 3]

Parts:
CN2: FCI-10103594-0001LF
R1, R3: 22Ω; R0402
R2: 1.5k; R0402

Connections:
D+1: R1.2; also elsewhere on the board
D+_IN_1: CN2.3 (D+), R1.1, R2.2
D-1: R3.2; also elsewhere on the board
D-_IN_1: CN2.2 (D-), R3.1
GND: CN2.5 (GND); also elsewhere on the board
V+: CN2.1 (VCC), R2.1; also elsewhere on the board

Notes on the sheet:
Connect VBUSx to the VBUS pin on the microcontroller
Connect D+x to the D+ pin on the microcontroller
Connect D-x to the D- pin on the microcontroller
The maximum capacitance on VBUS is 10µF and minimum is 1µF
IF DRAWING POWER FROM USB, CHECK THE VOLTAGE REGULATOR FOR CAPACITANCE

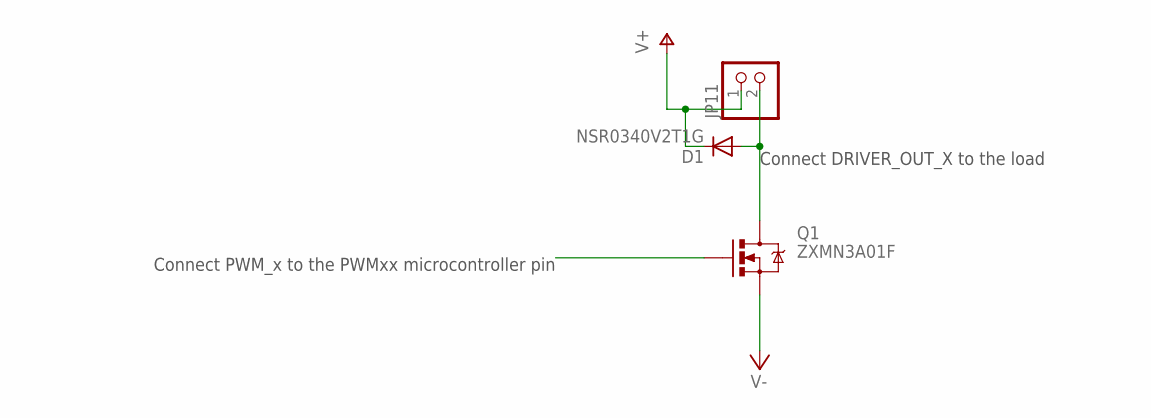
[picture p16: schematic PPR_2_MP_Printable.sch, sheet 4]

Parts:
D1: NSR0340V2T1G; SOD523
JP11: PINHD-1X2; 1X02
Q1: ZXMN3A01F; SOT23-3

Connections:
DRIVER_OUT_1: D1.A, JP11.2, Q1.3 (D)
PWM_1: Q1.1 (G); also elsewhere on the board
V+: D1.C, JP11.1; also elsewhere on the board
V-: Q1.2 (S); also elsewhere on the board

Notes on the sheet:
Connect PWM_x to the PWMxx microcontroller pin
Connect DRIVER_OUT_X to the load

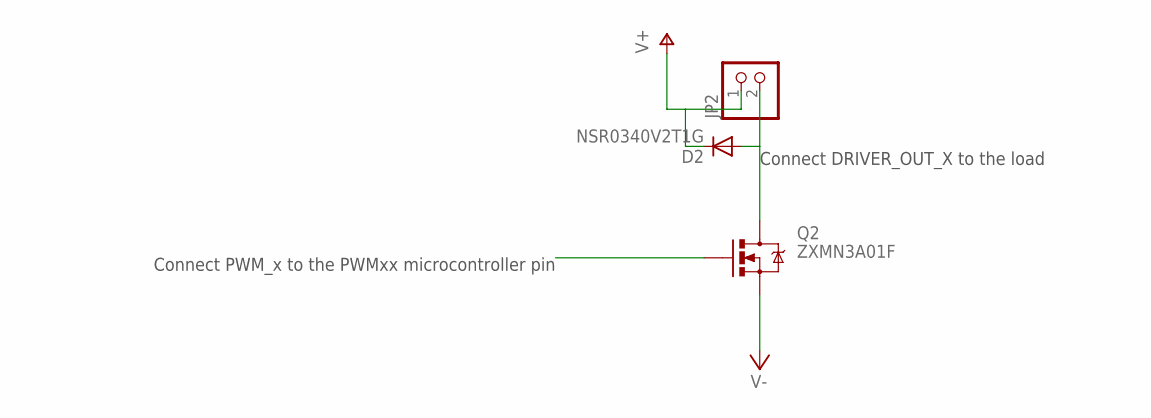
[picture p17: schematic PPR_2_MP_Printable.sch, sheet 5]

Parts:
D2: NSR0340V2T1G; SOD523
JP2: PINHD-1X2; 1X02
Q2: ZXMN3A01F; SOT23-3

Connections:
DRIVER_OUT_2: D2.A, JP2.2, Q2.3 (D)
PWM_2: Q2.1 (G); also elsewhere on the board
V+: D2.C, JP2.1; also elsewhere on the board
V-: Q2.2 (S); also elsewhere on the board

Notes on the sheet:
Connect PWM_x to the PWMxx microcontroller pin
Connect DRIVER_OUT_X to the load

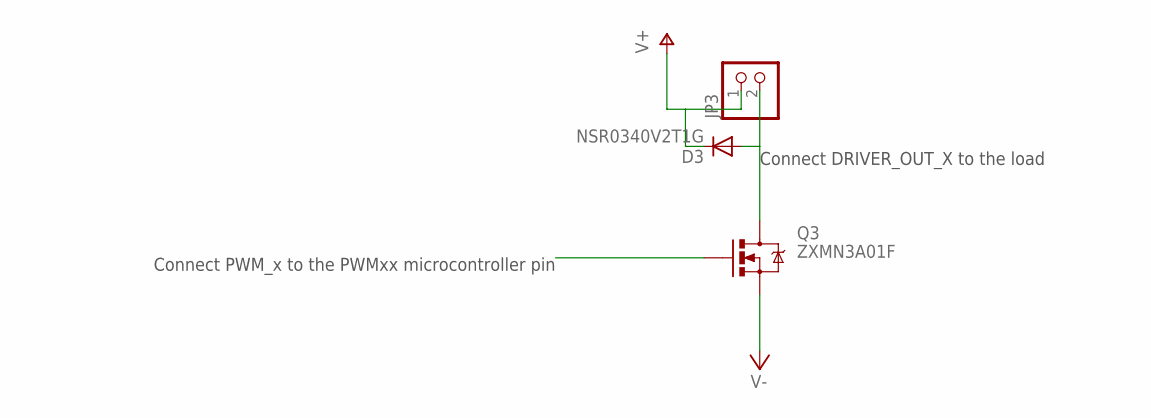
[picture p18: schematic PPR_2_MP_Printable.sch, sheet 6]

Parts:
D3: NSR0340V2T1G; SOD523
JP3: PINHD-1X2; 1X02
Q3: ZXMN3A01F; SOT23-3

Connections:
DRIVER_OUT_3: D3.A, JP3.2, Q3.3 (D)
PWM_3: Q3.1 (G); also elsewhere on the board
V+: D3.C, JP3.1; also elsewhere on the board
V-: Q3.2 (S); also elsewhere on the board

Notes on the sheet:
Connect PWM_x to the PWMxx microcontroller pin
Connect DRIVER_OUT_X to the load

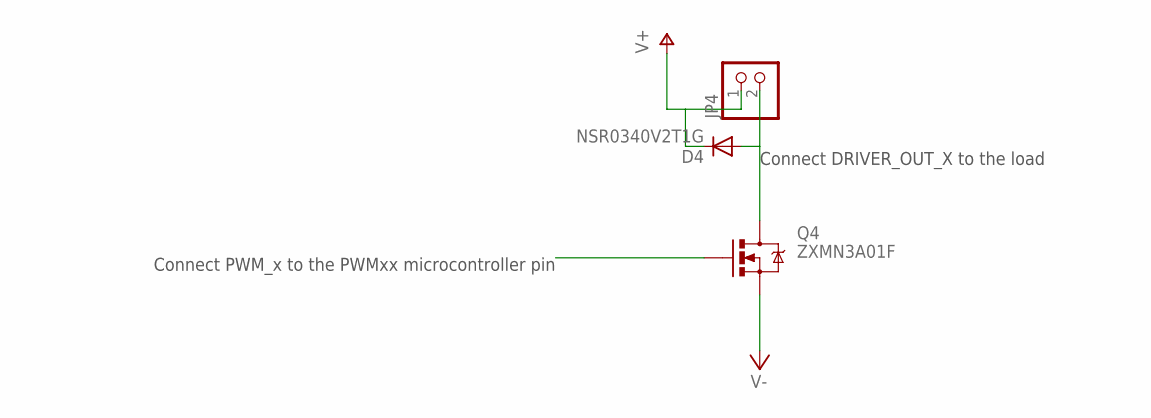
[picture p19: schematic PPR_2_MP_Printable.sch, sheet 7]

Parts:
D4: NSR0340V2T1G; SOD523
JP4: PINHD-1X2; 1X02
Q4: ZXMN3A01F; SOT23-3

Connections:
DRIVER_OUT_4: D4.A, JP4.2, Q4.3 (D)
PWM_4: Q4.1 (G); also elsewhere on the board
V+: D4.C, JP4.1; also elsewhere on the board
V-: Q4.2 (S); also elsewhere on the board

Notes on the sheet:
Connect PWM_x to the PWMxx microcontroller pin
Connect DRIVER_OUT_X to the load

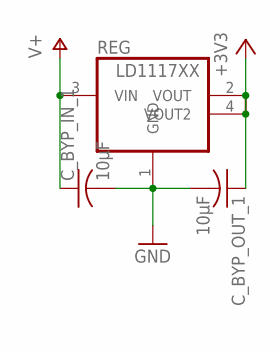
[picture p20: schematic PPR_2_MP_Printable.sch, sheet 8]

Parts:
C_BYP_IN_1: 10µF; C1206
C_BYP_OUT_1: 10µF; C0603
REG: LD1117XX; SOT-223

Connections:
+3V3: C_BYP_OUT_1.1, REG.2 (VOUT), REG.4 (VOUT2); also elsewhere on the board
GND: C_BYP_IN_1.2, C_BYP_OUT_1.2, REG.1 (GND); also elsewhere on the board
V+: C_BYP_IN_1.1, REG.3 (VIN); also elsewhere on the board

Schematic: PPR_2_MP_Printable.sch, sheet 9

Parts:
C_IMU_B_1: .1uF; C0603
C_IMU_CP_1: 2.2nF; C0603
C_IMU_FILT_1: .1uF; C0603
I2C_PULLUP_1, I2C_PULLUP_2: 10k; R0402
U5: TESTING_MPU-6050-1; TESTING_QFN-24-4MM2
VLOGIC_BYPASS_1: 10nF; C0603

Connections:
+3V3: C_IMU_B_1.2, I2C_PULLUP_1.2, I2C_PULLUP_2.2, U5.8 (VLOGIC), U5.13 (VDD), VLOGIC_BYPASS_1.2; also elsewhere on the board
CPOUT_1: C_IMU_CP_1.2, U5.20 (CPOUT)
GND: C_IMU_B_1.1, C_IMU_CP_1.1, C_IMU_FILT_1.1, U5.1 (CLKIN), U5.9 (AD0), U5.11 (FSYNC), U5.18 (GND), VLOGIC_BYPASS_1.1; also elsewhere on the board
IMU_IRQ_1: U5.12 (INT)
IMU_SCL_1: I2C_PULLUP_1.1, U5.23 (SCL); also elsewhere on the board
IMU_SDA_1: I2C_PULLUP_2.1, U5.24 (SDA); also elsewhere on the board
REGOUT_1: C_IMU_FILT_1.2, U5.10 (REGOUT)

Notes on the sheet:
I2C ADDR Select

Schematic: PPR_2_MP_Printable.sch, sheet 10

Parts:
JP10: PINHD-1X2; 1X02

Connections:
GND: JP10.2; also elsewhere on the board
V+: JP10.1; also elsewhere on the board

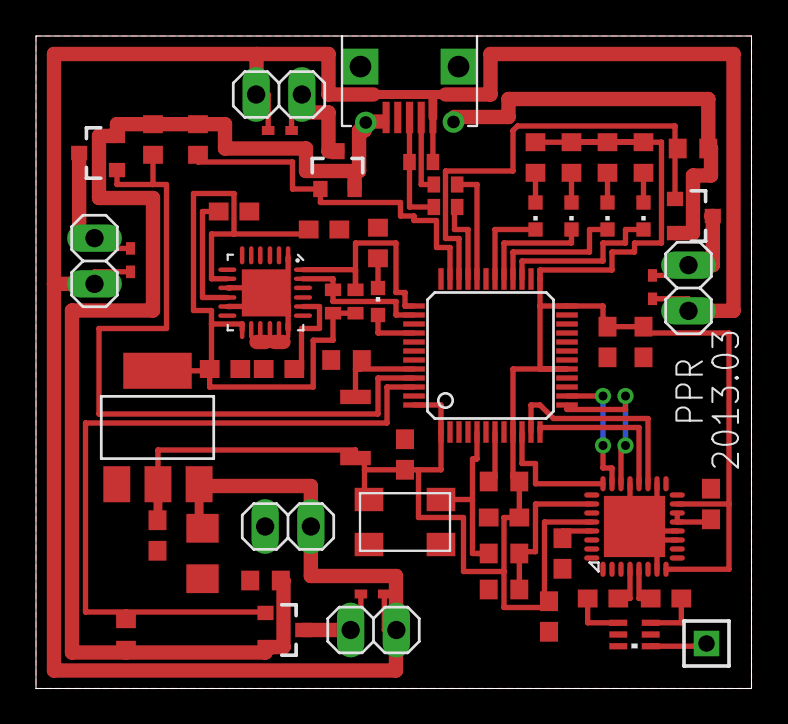
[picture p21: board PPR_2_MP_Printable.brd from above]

Board: 2 copper layers, 39.8 x 36.2 mm, 61 parts (0 on the bottom side), 46 nets.

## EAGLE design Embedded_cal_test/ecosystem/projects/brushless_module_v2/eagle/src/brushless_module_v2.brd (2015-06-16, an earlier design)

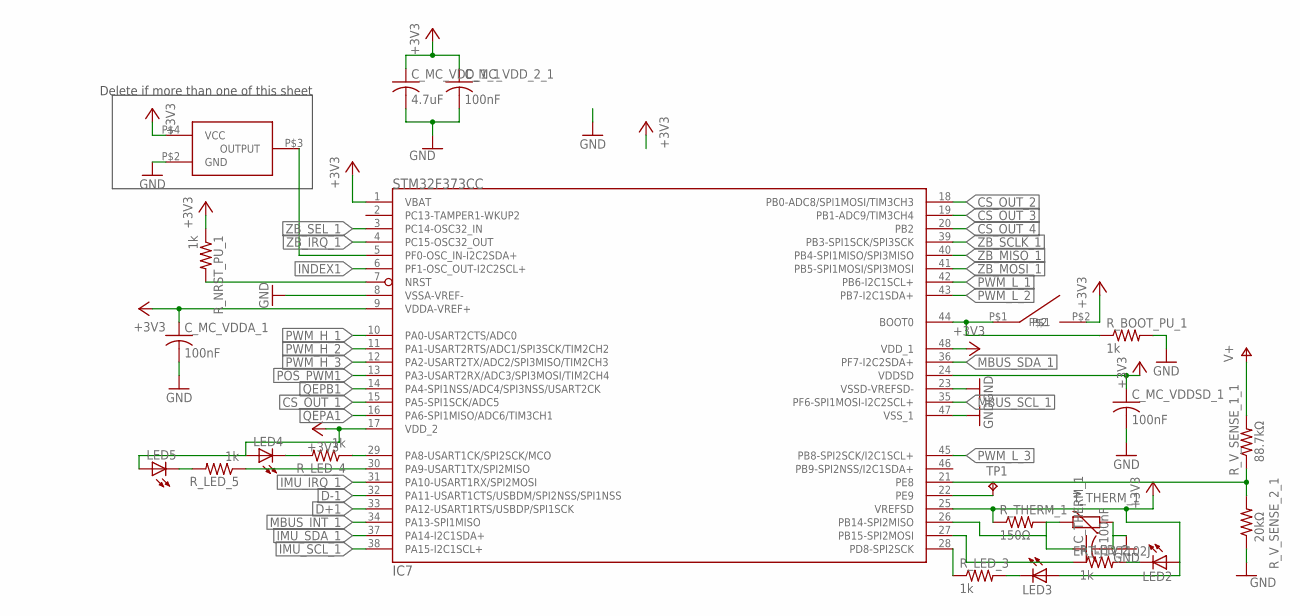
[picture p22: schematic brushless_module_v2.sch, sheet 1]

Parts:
C_MC_VDDA_1: 100nF; C0603
C_MC_VDDSD_1: 100nF; C0603
C_MC_VDD_1_1: 4.7uF; C0603
C_MC_VDD_2_1: 100nF; C0603
C_THERM_1: 100nF; C0603
IC7: STM32F373CC; LQFP48
LED2, LED3, LED4, LED5: LEDCHIPLED_0603; CHIPLED_0603
OSC1: FOX924B; 4-SMD_5X3.2
R_BOOT_PU_1: 1k; R0603
R_LED_2, R_LED_3, R_LED_4, R_LED_5: 1k; R0603
R_NRST_PU_1: 1k; R0603
R_THERM_1: 150Ω; R0603
R_V_SENSE_1_1: 88.7kΩ; R0603
R_V_SENSE_2_1: 20kΩ; R0603
SW1: B3U
TP1: TPTP10R; TP10R
T_THERM_1: ERT-J1VT102J; CT/CN0603

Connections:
16MHZ_3V3: IC7.5 (PF0-OSC_IN-I2C2SDA+), OSC1.P$3 (OUTPUT); also elsewhere on the board
+3V3: C_MC_VDDA_1.1, C_MC_VDDSD_1.1, C_MC_VDD_1_1.1, C_MC_VDD_2_1.1, IC7.1 (VBAT), IC7.9 (VDDA-VREF+), IC7.17 (VDD_2), IC7.24 (VDDSD), IC7.25 (VREFSD), IC7.48 (VDD_1), LED2.A, LED3.A, LED4.A, LED5.A, OSC1.P$4 (VCC), R_NRST_PU_1.1, R_THERM_1.1, SW1.P$2; also elsewhere on the board
BOOT0_1: IC7.44 (BOOT0), R_BOOT_PU_1.1, SW1.P$1
CS_OUT_1: IC7.15 (PA5-SPI1SCK/ADC5); also elsewhere on the board
CS_OUT_2: IC7.18 (PB0-ADC8/SPI1MOSI/TIM3CH3); also elsewhere on the board
CS_OUT_3: IC7.19 (PB1-ADC9/TIM3CH4); also elsewhere on the board
CS_OUT_4: IC7.20 (PB2); also elsewhere on the board
D+1: IC7.33 (PA12-USART1RTS/USBDP/SPI1SCK); also elsewhere on the board
D-1: IC7.32 (PA11-USART1CTS/USBDM/SPI2NSS/SPI1NSS); also elsewhere on the board
GND: C_MC_VDDA_1.2, C_MC_VDDSD_1.2, C_MC_VDD_1_1.2, C_MC_VDD_2_1.2, C_THERM_1.2, IC7.8 (VSSA-VREF-), IC7.23 (VSSD-VREFSD-), IC7.47 (VSS_1), OSC1.P$2 (GND), R_BOOT_PU_1.2, R_V_SENSE_2_1.1, T_THERM_1.1; also elsewhere on the board
IMU_IRQ_1: IC7.31 (PA10-USART1RX/SPI2MOSI); also elsewhere on the board
IMU_SCL_1: IC7.38 (PA15-I2C1SCL+); also elsewhere on the board
IMU_SDA_1: IC7.37 (PA14-I2C1SDA+); also elsewhere on the board
INDEX1: IC7.6 (PF1-OSC_OUT-I2C2SCL+); also elsewhere on the board
MBUS_INT_1: IC7.34 (PA13-SPI1MISO); also elsewhere on the board
MBUS_SCL_1: IC7.35 (PF6-SPI1MOSI-I2C2SCL+); also elsewhere on the board
MBUS_SDA_1: IC7.36 (PF7-I2C2SDA+); also elsewhere on the board
unnamed: IC7.21 (PE8), R_V_SENSE_1_1.1, R_V_SENSE_2_1.2
unnamed: LED2.C, R_LED_2.2
unnamed: LED3.C, R_LED_3.2
unnamed: IC7.27 (PB15-SPI2MOSI), R_LED_2.1
unnamed: IC7.28 (PD8-SPI2SCK), R_LED_3.1
unnamed: LED4.C, R_LED_4.2
unnamed: LED5.C, R_LED_5.2
unnamed: IC7.29 (PA8-USART1CK/SPI2SCK/MCO), R_LED_4.1
unnamed: IC7.30 (PA9-USART1TX/SPI2MISO), R_LED_5.1
unnamed: IC7.22 (PE9), TP1.TP
NRST_1: IC7.7 (NRST), R_NRST_PU_1.2
POS_PWM1: IC7.13 (PA3-USART2RX/ADC3/SPI3MOSI/TIM2CH4); also elsewhere on the board
PWM_H_1: IC7.10 (PA0-USART2CTS/ADC0); also elsewhere on the board
PWM_H_2: IC7.11 (PA1-USART2RTS/ADC1/SPI3SCK/TIM2CH2); also elsewhere on the board
PWM_H_3: IC7.12 (PA2-USART2TX/ADC2/SPI3MISO/TIM2CH3); also elsewhere on the board
PWM_L_1: IC7.42 (PB6-I2C1SCL+); also elsewhere on the board
PWM_L_2: IC7.43 (PB7-I2C1SDA+); also elsewhere on the board
PWM_L_3: IC7.45 (PB8-SPI2SCK/I2C1SCL+); also elsewhere on the board
QEPA1: IC7.16 (PA6-SPI1MISO/ADC6/TIM3CH1); also elsewhere on the board
QEPB1: IC7.14 (PA4-SPI1NSS/ADC4/SPI3NSS/USART2CK); also elsewhere on the board
THERM: C_THERM_1.1, IC7.26 (PB14-SPI2MISO), R_THERM_1.2, T_THERM_1.2
V+: R_V_SENSE_1_1.2; also elsewhere on the board
ZB_IRQ_1: IC7.4 (PC15-OSC32_OUT); also elsewhere on the board
ZB_MISO_1: IC7.40 (PB4-SPI1MISO/SPI3MISO); also elsewhere on the board
ZB_MOSI_1: IC7.41 (PB5-SPI1MOSI/SPI3MOSI); also elsewhere on the board
ZB_SCLK_1: IC7.39 (PB3-SPI1SCK/SPI3SCK); also elsewhere on the board
ZB_SEL_1: IC7.3 (PC14-OSC32_IN); also elsewhere on the board

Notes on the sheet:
Delete if more than one of this sheet

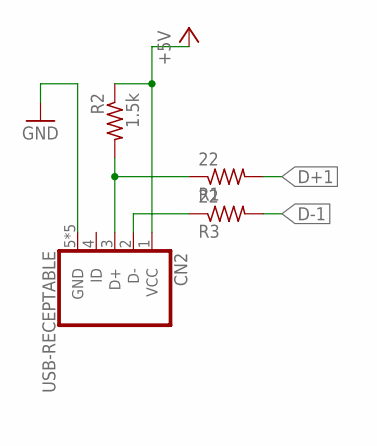
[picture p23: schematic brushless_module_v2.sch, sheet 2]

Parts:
CN2: USB-RECEPTABLE; FCI-10103594-0001LF
R1, R3: 22; R0603
R2: 1.5k; R0603

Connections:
+5V: CN2.1 (VCC), R2.1; also elsewhere on the board
D+1: R1.2; also elsewhere on the board
D+_IN_1: CN2.3 (D+), R1.1, R2.2
D-1: R3.2; also elsewhere on the board
D-_IN_1: CN2.2 (D-), R3.1
GND: CN2.5 (GND), CN2.P$1 (GND), CN2.P$2 (GND), CN2.P$3 (GND), CN2.P$4 (GND); also elsewhere on the board

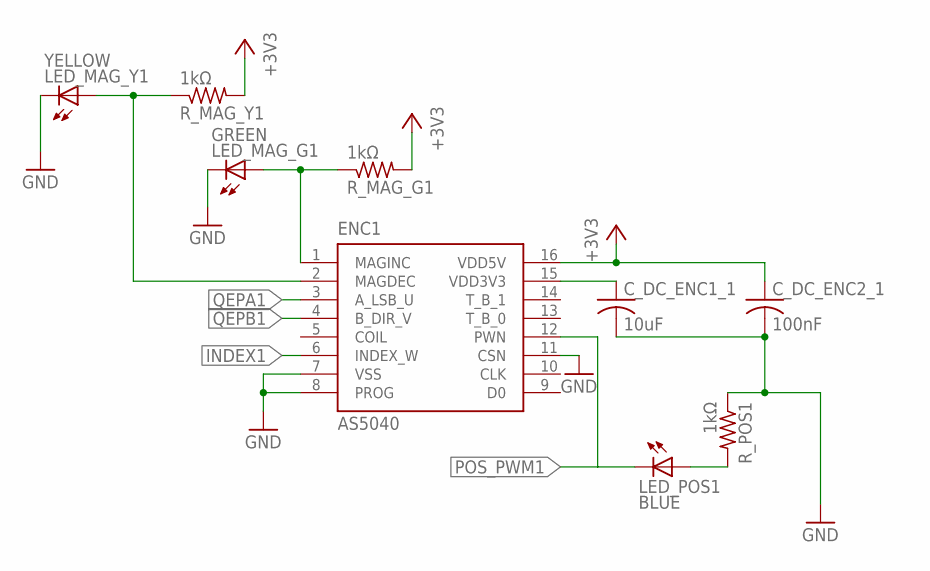
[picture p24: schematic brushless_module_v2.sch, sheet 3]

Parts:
C_DC_ENC1_1: 10uF; C0603
C_DC_ENC2_1: 100nF; C0603
ENC1: AS5040; SSOP16
LED_MAG_G1: GREEN; CHIP-LED0603
LED_MAG_Y1: YELLOW; CHIP-LED0603
LED_POS1: BLUE; CHIP-LED0603
R_MAG_G1: 1kΩ; R0603
R_MAG_Y1: 1kΩ; R0603
R_POS1: 1kΩ; R0603

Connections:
+3V3: C_DC_ENC2_1.1, ENC1.16 (VDD5V), R_MAG_G1.2, R_MAG_Y1.2; also elsewhere on the board
ENC_3V3_1: C_DC_ENC1_1.1, ENC1.15 (VDD3V3)
GND: C_DC_ENC1_1.2, C_DC_ENC2_1.2, ENC1.7 (VSS), ENC1.8 (PROG), ENC1.11 (CSN), LED_MAG_G1.C, LED_MAG_Y1.C, R_POS1.1; also elsewhere on the board
INDEX1: ENC1.6 (INDEX_W); also elsewhere on the board
MAGDEC1: ENC1.2 (MAGDEC), LED_MAG_Y1.A, R_MAG_Y1.1
MAGINC1: ENC1.1 (MAGINC), LED_MAG_G1.A, R_MAG_G1.1
unnamed: LED_POS1.A, R_POS1.2
POS_PWM1: ENC1.12 (PWN), LED_POS1.C; also elsewhere on the board
QEPA1: ENC1.3 (A_LSB_U); also elsewhere on the board
QEPB1: ENC1.4 (B_DIR_V); also elsewhere on the board


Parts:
BALUN1: 0896FB15A0100
CB1, CB2, CB3, CB4: 1µF; C0603
C_RF_CU1_1, C_RF_CU2_1: 68pF; C0603
JP1: Whip; 1X01M
RADIO1: AT86RF; QFNN32
R_CLK_VDIV1_1: 620Ω; R0603
R_CLK_VDIV2_1: 100Ω; R0603

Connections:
16MHZ_0V5_1: RADIO1.26 (XTAL1), R_CLK_VDIV1_1.1, R_CLK_VDIV2_1.2
16MHZ_3V3: R_CLK_VDIV1_1.2; also elsewhere on the board
+3V3: CB2.1, CB4.1, RADIO1.8 (/RST), RADIO1.15 (DEVDD), RADIO1.28 (EVDD); also elsewhere on the board
ANT1: BALUN1.1 (UNBALANCED), JP1.1
GND: BALUN1.2 (GND), BALUN1.5 (GND), BALUN1.6 (GND), CB1.2, CB2.2, CB3.2, CB4.2, RADIO1.3 (AVSS), RADIO1.6 (AVSS), RADIO1.7 (DVSS), RADIO1.11 (SLP_TR), RADIO1.12 (DVSS), RADIO1.16 (DVSS), RADIO1.18 (DVSS), RADIO1.21 (DVSS), RADIO1.27 (AVSS), RADIO1.30 (AVSS), RADIO1.31 (AVSS), RADIO1.32 (AVSS), RADIO1.EXP (AVSS), R_CLK_VDIV2_1.1; also elsewhere on the board
ZB_AVDD1: CB1.1, RADIO1.29 (AVDD)
ZB_BAL1_1: BALUN1.3 (BALANCED1), C_RF_CU1_1.2
ZB_BAL2_1: BALUN1.4 (BALANCED2), C_RF_CU2_1.2
ZB_DVDD1: CB3.1, RADIO1.13 (DVDD), RADIO1.14 (DVDD)
ZB_IRQ_1: RADIO1.24 (IRQ); also elsewhere on the board
ZB_MISO_1: RADIO1.20 (MISO); also elsewhere on the board
ZB_MOSI_1: RADIO1.22 (MOSI); also elsewhere on the board
ZB_RFN1: C_RF_CU2_1.1, RADIO1.4 (RFP)
ZB_RFP1: C_RF_CU1_1.1, RADIO1.5 (RFN)
ZB_SCLK_1: RADIO1.19 (SCLK); also elsewhere on the board
ZB_SEL_1: RADIO1.23 (\SEL); also elsewhere on the board


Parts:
C_IMU_B_1: .1uF; C0603
C_IMU_CP_1: 2.2nF; C0603
C_IMU_FILT_1: .1uF; C0603
I2C_PULLUP_1, I2C_PULLUP_2: 1k; R0603
U$10: MPU-6050; QFN24
VLOGIC_BYPASS_1: 10nF; C0603

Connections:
+3V3: C_IMU_B_1.1, I2C_PULLUP_1.2, I2C_PULLUP_2.2, U$10.P$8 (VL), U$10.P$13 (VDD), VLOGIC_BYPASS_1.1; also elsewhere on the board
CPOUT_1: C_IMU_CP_1.1, U$10.P$20 (CPOUT)
GND: C_IMU_B_1.2, C_IMU_CP_1.2, C_IMU_FILT_1.2, U$10.P$1 (CLKIN), U$10.P$2 (NC), U$10.P$3 (NC), U$10.P$4 (NC), U$10.P$5 (NC), U$10.P$9 (AD0), U$10.P$11 (FSYNC), U$10.P$14 (NC), U$10.P$15 (NC), U$10.P$16 (NC), U$10.P$17 (NC), U$10.P$18 (GND), U$10.P$25 (GND), VLOGIC_BYPASS_1.2; also elsewhere on the board
IMU_IRQ_1: U$10.P$12 (INT); also elsewhere on the board
IMU_SCL_1: I2C_PULLUP_1.1, U$10.P$23 (SCL); also elsewhere on the board
IMU_SDA_1: I2C_PULLUP_2.1, U$10.P$24 (SDA); also elsewhere on the board
REGOUT_1: C_IMU_FILT_1.1, U$10.P$10 (REGOUT)


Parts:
CIN1_1, CIN2_1: 10µF; C0805
COUT1_1, COUT2_1: 22µF; C0603
C_BOOST1: 22nF; C0603
L_REG1: 4.7µH; VLC5045
SW_REG1: MCP16323; QFN16

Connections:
+3V3: COUT1_1.1, COUT2_1.1, L_REG1.2, SW_REG1.5 (VFB); also elsewhere on the board
BOOST1: C_BOOST1.1, SW_REG1.10 (BOOST)
GND: CIN1_1.2, CIN2_1.2, COUT1_1.2, COUT2_1.2, SW_REG1.4 (SGND), SW_REG1.14 (PGND), SW_REG1.15 (PGND), SW_REG1.TH (SGND); also elsewhere on the board
SW1: C_BOOST1.2, L_REG1.1, SW_REG1.1 (SW), SW_REG1.12 (SW), SW_REG1.13 (SW), SW_REG1.16 (SW)
V+: CIN1_1.1, CIN2_1.1, SW_REG1.2 (VIN), SW_REG1.3 (VIN), SW_REG1.11 (VIN); also elsewhere on the board


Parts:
C1: 150µF; D/7343-31R
D_UV_1: PMEG2005EJ,115; SOD323-W
MMSZ4684T1G: D-SOD123; SOD123
U$13: REG_SOT223LD1118XX; SOT-223

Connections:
+3V3: MMSZ4684T1G.1 (C), U$13.1 (VOUT); also elsewhere on the board
GND: C1.-, D_UV_1.A, MMSZ4684T1G.2 (A), U$13.2 (GND), U$13.4 (GND); also elsewhere on the board
V+: C1.+, D_UV_1.C, U$13.3 (VIN); also elsewhere on the board

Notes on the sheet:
Default is +3V3, change here!


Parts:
D_INV_FB_H1: NSR0340V2T1G; SOD523
D_INV_FB_L1: NSR0340V2T1G; SOD523
PMF290XN_1: PMF290XN; SOT323
R_INV_PD1: 100kΩ; R0603; PART# RNCP0603FTD825RCT-ND
R_INV_PU1: 2kΩ; R0603
R_LIM_H_1_1: 800Ω; R0603
R_LIM_H_2_1: 100Ω; R0603
R_LIM_L_1_1: 800Ω; R0603
R_LIM_L_2_1: 100Ω; R0603
U$1: SIR466DP-T1-GE3; S0-8-POWERPAK
U$2: SI7139DP-T1-GE3; S0-8-POWERPAK
ZXGD3004E6_H_1, ZXGD3004E6_L_1: ZXGD3004E6; SOT23-6

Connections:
GATE_DRV_HIGH_IN1: PMF290XN_1.1 (C), R_INV_PU1.1, ZXGD3004E6_H_1.2 (IN1), ZXGD3004E6_H_1.5 (IN2)
GATE_DRV_LOW_IN1: R_INV_PD1.1, R_LIM_L_1_1.1, ZXGD3004E6_L_1.2 (IN1), ZXGD3004E6_L_1.5 (IN2)
GND: D_INV_FB_L1.A, PMF290XN_1.3 (E), R_INV_PD1.2, U$1.1 (S), U$1.2 (S), U$1.3 (S), ZXGD3004E6_H_1.3 (GND), ZXGD3004E6_L_1.3 (GND); also elsewhere on the board
INV_HIGH_GATE1: R_LIM_H_2_1.2, U$2.4 (G)
INV_HIGH_GSS1: R_LIM_H_2_1.1, ZXGD3004E6_H_1.4 (SINK), ZXGD3004E6_H_1.6 (SOURCE)
INV_LOW_GATE1: R_LIM_L_2_1.2, U$1.4 (G)
INV_LOW_GSS1: R_LIM_L_2_1.1, ZXGD3004E6_L_1.4 (SINK), ZXGD3004E6_L_1.6 (SOURCE)
INV_OUT1: D_INV_FB_H1.A, D_INV_FB_L1.C, U$1.5 (D), U$1.6 (D), U$1.7 (D), U$1.8 (D), U$1.P$1 (D), U$2.5 (D), U$2.6 (D), U$2.7 (D), U$2.8 (D), U$2.P$1 (D); also elsewhere on the board
unnamed: PMF290XN_1.2 (B), R_LIM_H_1_1.1
PWM_H_1: R_LIM_H_1_1.2; also elsewhere on the board
PWM_L_1: R_LIM_L_1_1.2; also elsewhere on the board
V+: D_INV_FB_H1.C, R_INV_PU1.2, U$2.1 (S), U$2.2 (S), U$2.3 (S), ZXGD3004E6_H_1.1 (VCC), ZXGD3004E6_L_1.1 (VCC); also elsewhere on the board

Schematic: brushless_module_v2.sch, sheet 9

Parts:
D_INV_FB_H2: NSR0340V2T1G; SOD523
D_INV_FB_L2: NSR0340V2T1G; SOD523
PMF290XN_2: PMF290XN; SOT323
R_INV_PD2: 100kΩ; R0603; PART# RNCP0603FTD825RCT-ND
R_INV_PU2: 2kΩ; R0603
R_LIM_H_1_2: 800Ω; R0603
R_LIM_H_2_2: 100Ω; R0603
R_LIM_L_1_2: 800Ω; R0603
R_LIM_L_2_2: 100Ω; R0603
U$3: SIR466DP-T1-GE3; S0-8-POWERPAK
U$4: SI7139DP-T1-GE3; S0-8-POWERPAK
ZXGD3004E6_H_2, ZXGD3004E6_L_2: ZXGD3004E6; SOT23-6

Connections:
GATE_DRV_HIGH_IN2: PMF290XN_2.1 (C), R_INV_PU2.1, ZXGD3004E6_H_2.2 (IN1), ZXGD3004E6_H_2.5 (IN2)
GATE_DRV_LOW_IN2: R_INV_PD2.1, R_LIM_L_1_2.1, ZXGD3004E6_L_2.2 (IN1), ZXGD3004E6_L_2.5 (IN2)
GND: D_INV_FB_L2.A, PMF290XN_2.3 (E), R_INV_PD2.2, U$3.1 (S), U$3.2 (S), U$3.3 (S), ZXGD3004E6_H_2.3 (GND), ZXGD3004E6_L_2.3 (GND); also elsewhere on the board
INV_HIGH_GATE2: R_LIM_H_2_2.2, U$4.4 (G)
INV_HIGH_GSS2: R_LIM_H_2_2.1, ZXGD3004E6_H_2.4 (SINK), ZXGD3004E6_H_2.6 (SOURCE)
INV_LOW_GATE2: R_LIM_L_2_2.2, U$3.4 (G)
INV_LOW_GSS2: R_LIM_L_2_2.1, ZXGD3004E6_L_2.4 (SINK), ZXGD3004E6_L_2.6 (SOURCE)
INV_OUT2: D_INV_FB_H2.A, D_INV_FB_L2.C, U$3.5 (D), U$3.6 (D), U$3.7 (D), U$3.8 (D), U$3.P$1 (D), U$4.5 (D), U$4.6 (D), U$4.7 (D), U$4.8 (D), U$4.P$1 (D); also elsewhere on the board
unnamed: PMF290XN_2.2 (B), R_LIM_H_1_2.1
PWM_H_2: R_LIM_H_1_2.2; also elsewhere on the board
PWM_L_2: R_LIM_L_1_2.2; also elsewhere on the board
V+: D_INV_FB_H2.C, R_INV_PU2.2, U$4.1 (S), U$4.2 (S), U$4.3 (S), ZXGD3004E6_H_2.1 (VCC), ZXGD3004E6_L_2.1 (VCC); also elsewhere on the board

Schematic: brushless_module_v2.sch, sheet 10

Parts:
D_INV_FB_H3: NSR0340V2T1G; SOD523
D_INV_FB_L3: NSR0340V2T1G; SOD523
PMF290XN_3: PMF290XN; SOT323
R_INV_PD3: 100kΩ; R0603; PART# RNCP0603FTD825RCT-ND
R_INV_PU3: 2kΩ; R0603
R_LIM_H_1_3: 800Ω; R0603
R_LIM_H_2_3: 100Ω; R0603
R_LIM_L_1_3: 800Ω; R0603
R_LIM_L_2_3: 100Ω; R0603
U$5: SIR466DP-T1-GE3; S0-8-POWERPAK
U$6: SI7139DP-T1-GE3; S0-8-POWERPAK
ZXGD3004E6_H_3, ZXGD3004E6_L_3: ZXGD3004E6; SOT23-6

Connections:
GATE_DRV_HIGH_IN3: PMF290XN_3.1 (C), R_INV_PU3.1, ZXGD3004E6_H_3.2 (IN1), ZXGD3004E6_H_3.5 (IN2)
GATE_DRV_LOW_IN3: R_INV_PD3.1, R_LIM_L_1_3.1, ZXGD3004E6_L_3.2 (IN1), ZXGD3004E6_L_3.5 (IN2)
GND: D_INV_FB_L3.A, PMF290XN_3.3 (E), R_INV_PD3.2, U$5.1 (S), U$5.2 (S), U$5.3 (S), ZXGD3004E6_H_3.3 (GND), ZXGD3004E6_L_3.3 (GND); also elsewhere on the board
INV_HIGH_GATE3: R_LIM_H_2_3.2, U$6.4 (G)
INV_HIGH_GSS3: R_LIM_H_2_3.1, ZXGD3004E6_H_3.4 (SINK), ZXGD3004E6_H_3.6 (SOURCE)
INV_LOW_GATE3: R_LIM_L_2_3.2, U$5.4 (G)
INV_LOW_GSS3: R_LIM_L_2_3.1, ZXGD3004E6_L_3.4 (SINK), ZXGD3004E6_L_3.6 (SOURCE)
INV_OUT3: D_INV_FB_H3.A, D_INV_FB_L3.C, U$5.5 (D), U$5.6 (D), U$5.7 (D), U$5.8 (D), U$5.P$1 (D), U$6.5 (D), U$6.6 (D), U$6.7 (D), U$6.8 (D), U$6.P$1 (D); also elsewhere on the board
unnamed: PMF290XN_3.2 (B), R_LIM_H_1_3.1
PWM_H_3: R_LIM_H_1_3.2; also elsewhere on the board
PWM_L_3: R_LIM_L_1_3.2; also elsewhere on the board
V+: D_INV_FB_H3.C, R_INV_PU3.2, U$6.1 (S), U$6.2 (S), U$6.3 (S), ZXGD3004E6_H_3.1 (VCC), ZXGD3004E6_L_3.1 (VCC); also elsewhere on the board

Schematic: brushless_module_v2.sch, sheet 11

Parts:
CS_1: INA21X; SC70
C_CS_DC_1: 100nF; C0603
R_CS_1: 1mΩ; R1206

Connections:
CS_OUT_1: CS_1.P6 (OUT); also elsewhere on the board
GND: CS_1.P2 (GND), C_CS_DC_1.2; also elsewhere on the board
INV_OUT1: CS_1.P4 (IN+), R_CS_1.2; also elsewhere on the board
MOTOR_1: CS_1.P5 (IN-), R_CS_1.1; also elsewhere on the board
V+: CS_1.P3 (V+), C_CS_DC_1.1; also elsewhere on the board
V_REF_CS: CS_1.P1 (REF); also elsewhere on the board

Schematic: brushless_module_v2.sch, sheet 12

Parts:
CS_2: INA21X; SC70
C_CS_DC_2: 100nF; C0603
R_CS_2: 1mΩ; R1206

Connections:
CS_OUT_2: CS_2.P6 (OUT); also elsewhere on the board
GND: CS_2.P2 (GND), C_CS_DC_2.2; also elsewhere on the board
INV_OUT2: CS_2.P5 (IN-), R_CS_2.2; also elsewhere on the board
MOTOR_2: CS_2.P4 (IN+), R_CS_2.1; also elsewhere on the board
V+: CS_2.P3 (V+), C_CS_DC_2.1; also elsewhere on the board
V_REF_CS: CS_2.P1 (REF); also elsewhere on the board

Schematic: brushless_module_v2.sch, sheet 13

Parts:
CS_3: INA21X; SC70
C_CS_DC_3: 100nF; C0603
R_CS_3: 1mΩ; R1206

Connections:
CS_OUT_3: CS_3.P6 (OUT); also elsewhere on the board
GND: CS_3.P2 (GND), C_CS_DC_3.2; also elsewhere on the board
INV_OUT3: CS_3.P4 (IN+), R_CS_3.2; also elsewhere on the board
MOTOR_3: CS_3.P5 (IN-), R_CS_3.1; also elsewhere on the board
V+: CS_3.P3 (V+), C_CS_DC_3.1; also elsewhere on the board
V_REF_CS: CS_3.P1 (REF); also elsewhere on the board

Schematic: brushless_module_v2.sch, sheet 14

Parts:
CS_4: INA21X; SC70
C_CS_DC_4: 100nF; C0603
C_S_1: 6.47uF; C0603
R_CS_4: 1mΩ; R1206
R_CS_REF1_4, R_CS_REF2_4: 10kΩ; R0603
R_S1_1, R_S2_1: 10Ω; R0603

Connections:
+3V3: R_CS_REF1_4.2; also elsewhere on the board
CS_OUT_4: CS_4.P6 (OUT); also elsewhere on the board
GND: CS_4.P2 (GND), C_CS_DC_4.2, R_CS_REF2_4.1; also elsewhere on the board
IN+_1: CS_4.P4 (IN+), C_S_1.1, R_S2_1.1
IN-_1: CS_4.P5 (IN-), C_S_1.2, R_S1_1.1
V+: R_CS_4.1, R_S1_1.2; also elsewhere on the board
V_BATT: CS_4.P3 (V+), C_CS_DC_4.1, R_CS_4.2, R_S2_1.2; also elsewhere on the board
V_REF_CS: CS_4.P1 (REF), R_CS_REF1_4.1, R_CS_REF2_4.2; also elsewhere on the board

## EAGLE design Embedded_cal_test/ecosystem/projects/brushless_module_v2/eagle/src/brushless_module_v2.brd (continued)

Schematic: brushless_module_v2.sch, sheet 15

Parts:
C2: 0.1uF; C0603
C3: 10uF; C0603
D_OV_1: PMEG2005EJ,115; SOD323-W
FPF2123: FPF2123; SOT23-5L
R4: 1MΩ; R0603
R6: 604Ω; R0603

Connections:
+5V: C3.1, FPF2123.1 (VIN), FPF2123.3 (ON); also elsewhere on the board
GND: C2.2, C3.2, FPF2123.2 (GND), R4.1, R6.1; also elsewhere on the board
LOAD_ISET_1: FPF2123.4 (ISET), R6.2
unnamed: D_OV_1.A, FPF2123.5 (VOUT), R4.2
V+: C2.1, D_OV_1.C; also elsewhere on the board

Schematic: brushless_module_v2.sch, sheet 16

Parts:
R11, R12: 1k; R0603
U$7: SM05B-GHS-TB

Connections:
+3V3: R11.2, R12.2, U$7.P$3 (3); also elsewhere on the board
GND: U$7.P$5 (5); also elsewhere on the board
MBUS_INT_1: U$7.P$1 (1); also elsewhere on the board
MBUS_SCL_1: R12.1, U$7.P$4 (4); also elsewhere on the board
MBUS_SDA_1: R11.1, U$7.P$2 (2); also elsewhere on the board

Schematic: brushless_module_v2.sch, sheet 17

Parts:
U$8: DEANS-MICRO-2PIN
U$9: DEANS-MICRO-3PIN

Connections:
GND: U$8.P$2 (2); also elsewhere on the board
MOTOR_1: U$9.P$1 (1); also elsewhere on the board
MOTOR_2: U$9.P$2 (2); also elsewhere on the board
MOTOR_3: U$9.P$3 (3); also elsewhere on the board
V_BATT: U$8.P$1 (1); also elsewhere on the board



Board: 2 copper layers, 40.0 x 40.0 mm, 134 parts (60 on the bottom side), 96 nets.

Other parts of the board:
U$11: PENN_ENGINEERING
U$12: MODLAB

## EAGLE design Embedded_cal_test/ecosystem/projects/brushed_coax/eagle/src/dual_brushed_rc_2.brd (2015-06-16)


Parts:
C_MC_VDDA_1: 1 µF; C0402
C_MC_VDD_1_1: 3.3 µF; C0603
C_MC_VDD_2_1, C_MC_VDD_3_1: 1 µF; C0402
R_BOOT_PU_1: 33 kΩ; R0402
U$1: STM32F303CX; LQFP48

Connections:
16MHZ_CMOS: U$1.5 (PF0-OSC_IN); also elsewhere on the board
+3V3: C_MC_VDDA_1.1, C_MC_VDD_1_1.1, C_MC_VDD_2_1.1, C_MC_VDD_3_1.1, U$1.1 (VBAT), U$1.9 (VDDA/VREF+), U$1.24 (VDD_2), U$1.36 (VDD_3), U$1.48 (VDD_1); also elsewhere on the board
AMP_SENSE: U$1.25 (PB12); also elsewhere on the board
BLUE_LED: U$1.37 (PA14); also elsewhere on the board
BOOT0: R_BOOT_PU_1.1, U$1.44 (BOOT0); also elsewhere on the board
EXT_RX: U$1.40 (PB4); also elsewhere on the board
EXT_TX: U$1.39 (PB3); also elsewhere on the board
GND: C_MC_VDDA_1.2, C_MC_VDD_1_1.2, C_MC_VDD_2_1.2, C_MC_VDD_3_1.2, R_BOOT_PU_1.2, U$1.8 (VSSA/VREF-), U$1.23 (VSS_2), U$1.35 (VSS_3), U$1.47 (VSS_1); also elsewhere on the board
GPIO,#,+,IO.B,2: U$1.20 (PB2)
GPIO,#,+,IO.C,14: U$1.3 (PC14-OSC32_IN)
GPIO,#,+,IO.C,15: U$1.4 (PC15-OSC32_OUT)
GPIO,#,+,IO/PWM,3,+,IO,TIMER,2,1/TXRX,#,-,O,UART,3,7.B,10: U$1.21 (PB10)
GPIO,#,+,IO/PWM,3,+,IO,TIMER,3,2/PWM_N,2,+,O,TIMER,8,4/PWM_N,2,+,O,TIMER,1,6.B,0: U$1.18 (PB0)
GPIO,#,+,IO/PWM,4,+,IO,TIMER,2,1/TXRX,#,-,I,UART,3,7.B,11: U$1.22 (PB11)
GPIO,#,+,IO/PWM_N,1,+,O,TIMER,1,4.C,13: U$1.2 (PC13)
GPIO,#,+,IO/SCL,#,+,IO,I2C,2,4.F,1: U$1.6 (PF1-OSC_OUT)
GPIO,#,+,IO/SDA,+,IO,I2C,2,4/PWM,3,+,IO,TIMER,1,6/TXRX,-,I,UART,1,7/PWM,4,+,IO,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: U$1.31 (PA10)
GREEN_LED: U$1.41 (PB5); also elsewhere on the board
HALL_SIG: U$1.19 (PB1); also elsewhere on the board
IMU_SCL: U$1.45 (PB8); also elsewhere on the board
IMU_SDA: U$1.46 (PB9); also elsewhere on the board
IN_1_HIGH: U$1.26 (PB13); also elsewhere on the board
IN_1_LOW: U$1.29 (PA8); also elsewhere on the board
IN_2_HIGH: U$1.27 (PB14); also elsewhere on the board
IN_2_LOW: U$1.30 (PA9); also elsewhere on the board
PA0: U$1.10 (PA0)
PA1: U$1.11 (PA1); also elsewhere on the board
PA2: U$1.12 (PA2); also elsewhere on the board
RED_LED: U$1.42 (PB6); also elsewhere on the board
USB_D+: U$1.33 (PA12); also elsewhere on the board
USB_D-: U$1.32 (PA11); also elsewhere on the board
VOLT_SENSE: U$1.28 (PB15); also elsewhere on the board
YELLOW_LED: U$1.43 (PB7); also elsewhere on the board
ZIG_IRQ: U$1.13 (PA3); also elsewhere on the board
ZIG_MISO: U$1.16 (PA6); also elsewhere on the board
ZIG_MOSI: U$1.17 (PA7); also elsewhere on the board
ZIG_SCK: U$1.15 (PA5); also elsewhere on the board
ZIG_SS: U$1.14 (PA4); also elsewhere on the board

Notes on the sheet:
If using A2D


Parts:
BALUN1: 0896FB15A0100
C5: 100 pF; C0402
CB1, CB2, CB3: 1 µF; C0402
JP1: Whip; 1X01
R_CLK_VDIV1_1: 1.2 kΩ; R0402
R_CLK_VDIV2_1: 220 Ω; R0402
U$51: AT86RF; QFNN32

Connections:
16MHZ_0V5_1: R_CLK_VDIV1_1.1, R_CLK_VDIV2_1.2, U$51.26 (XTAL1)
16MHZ_CMOS: R_CLK_VDIV1_1.2; also elsewhere on the board
+3V3: CB2.1, U$51.8 (/RST), U$51.15 (DEVDD), U$51.28 (EVDD); also elsewhere on the board
GND: BALUN1.2 (GND), BALUN1.5 (GND), BALUN1.6 (GND), CB1.2, CB2.2, CB3.2, R_CLK_VDIV2_1.1, U$51.3 (AVSS), U$51.6 (AVSS), U$51.7 (DVSS), U$51.11 (SLP_TR), U$51.12 (DVSS), U$51.16 (DVSS), U$51.18 (DVSS), U$51.21 (DVSS), U$51.27 (AVSS), U$51.30 (AVSS), U$51.31 (AVSS), U$51.32 (AVSS), U$51.EXP (AVSS); also elsewhere on the board
unnamed: BALUN1.1 (UNBALANCED), C5.2
unnamed: C5.1, JP1.1
unnamed: CB3.1, U$51.13 (DVDD), U$51.14 (DVDD)
unnamed: CB1.1, U$51.29 (AVDD)
unnamed: BALUN1.4 (BALANCED2), U$51.4 (RFP)
unnamed: BALUN1.3 (BALANCED1), U$51.5 (RFN)
ZIG_IRQ: U$51.24 (IRQ); also elsewhere on the board
ZIG_MISO: U$51.20 (MISO); also elsewhere on the board
ZIG_MOSI: U$51.22 (MOSI); also elsewhere on the board
ZIG_SCK: U$51.19 (SCLK); also elsewhere on the board
ZIG_SS: U$51.23 (\SEL); also elsewhere on the board


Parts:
C6: 10 nF; C0402
U$54: ASTX-H11

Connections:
16MHZ_CMOS: U$54.P$3 (OUT); also elsewhere on the board
+3V3: C6.1, U$54.P$4 (VDD); also elsewhere on the board
GND: C6.2, U$54.P$2 (GND); also elsewhere on the board


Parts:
C_IMU_B_1: 100 nF; C0402
C_IMU_CP_1: 2.2 nF; C0402
C_IMU_FILT_1: 100 nF; C0402
I2C_PULLUP_1, I2C_PULLUP_2: 10 kΩ; R0402
U$46: MPU-6050; QFN24
VLOGIC_BYPASS_1: 10 nF; C0402

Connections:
+3V3: C_IMU_B_1.1, I2C_PULLUP_1.2, I2C_PULLUP_2.2, U$46.P$8 (VL), U$46.P$13 (VDD), VLOGIC_BYPASS_1.1; also elsewhere on the board
GND: C_IMU_B_1.2, C_IMU_CP_1.2, C_IMU_FILT_1.2, U$46.P$1 (CLKIN), U$46.P$2 (NC), U$46.P$3 (NC), U$46.P$4 (NC), U$46.P$5 (NC), U$46.P$9 (AD0), U$46.P$11 (FSYNC), U$46.P$14 (NC), U$46.P$15 (NC), U$46.P$16 (NC), U$46.P$17 (NC), U$46.P$18 (GND), U$46.P$25 (GND), VLOGIC_BYPASS_1.2; also elsewhere on the board
IMU_INT: U$46.P$12 (INT)
IMU_SCL: I2C_PULLUP_1.1, U$46.P$23 (SCL); also elsewhere on the board
IMU_SDA: I2C_PULLUP_2.1, U$46.P$24 (SDA); also elsewhere on the board
unnamed: C_IMU_CP_1.1, U$46.P$20 (CPOUT)
REGOUT_1: C_IMU_FILT_1.1, U$46.P$10 (REGOUT)


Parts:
C1: 2.2 µF; C0603
C2, C3: 100 nF; C0402
C4: 47 µF; C0805
D1, D2, D3, D4: BAS 52-02V; SOD523
R1: 6.8 kΩ; R0402
R2: 2.7 kΩ; R0402
R3: 1 kΩ; R0402
U1: DRV8850_RGY_24; RGY_24

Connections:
+3V3: C1.1, C2.1, R1.2, U1.15 (LDOOUT); also elsewhere on the board
AMP_SENSE: R3.2, U1.16 (VPROPI); also elsewhere on the board
GND: C1.2, C3.2, C4.2, D3.A, D4.A, R2.1, R3.1, U1.1 (GND_4), U1.11 (SR), U1.12 (GND_3), U1.13 (GND), U1.24 (GND_2), U1.PPAD (GND_5); also elsewhere on the board
HALF_OUT_1: D2.A, D4.C, U1.2 (OUT1_2), U1.3 (OUT1_3), U1.4 (OUT1); also elsewhere on the board
HALF_OUT_2: D1.A, D3.C, U1.21 (OUT2), U1.22 (OUT2_2), U1.23 (OUT2_3); also elsewhere on the board
IN_1_HIGH: U1.5 (IN1H); also elsewhere on the board
IN_1_LOW: U1.6 (IN1L); also elsewhere on the board
IN_2_HIGH: U1.7 (IN2H); also elsewhere on the board
IN_2_LOW: U1.8 (IN2L); also elsewhere on the board
unnamed: R1.1, R2.2, U1.14 (LDOFB)
unnamed: C2.2, U1.17 (VCP)
V+: C3.1, C4.1, D1.C, D2.C, U1.9 (NSLEEP), U1.10 (LDOEN), U1.18 (VCC_2), U1.19 (VCC_3), U1.20 (VCC); also elsewhere on the board


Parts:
JP2: M02-JST-2-PTH-NO_SILK; JST-2-PTH-NS
R9, R10: 33 kΩ; R0402
TP1, TP2, TP3, TP4, TP5, TP6, TP7: TPTP10SQ; TP10SQ
U$55, U$58, U$59, U$60: PADSURF; PAD_1_SURF

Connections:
+3V3: TP1.TP; also elsewhere on the board
EXT_RX: TP4.TP; also elsewhere on the board
EXT_TX: TP5.TP; also elsewhere on the board
GND: JP2.1, R10.1, TP2.TP, U$59.1, U$60.1; also elsewhere on the board
HALF_OUT_1: U$58.1; also elsewhere on the board
HALF_OUT_2: U$55.1; also elsewhere on the board
HALL_SIG: TP3.TP; also elsewhere on the board
PA1: TP6.TP; also elsewhere on the board
PA2: TP7.TP; also elsewhere on the board
V+: JP2.2, R9.2; also elsewhere on the board
VOLT_SENSE: R9.1, R10.2; also elsewhere on the board


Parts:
U$56: SM06B-SRSS-TB

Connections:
+5V: U$56.P$1 (1)
BOOT0: U$56.P$5 (5); also elsewhere on the board
GND: U$56.P$4 (4); also elsewhere on the board
USB_D+: U$56.P$3 (3); also elsewhere on the board
USB_D-: U$56.P$2 (2); also elsewhere on the board
V+: U$56.P$6 (6); also elsewhere on the board


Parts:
BLUE_LED: LEDCHIPLED_0603; CHIPLED_0603
GREEN_LED: LEDCHIPLED_0603; CHIPLED_0603
R4, R5, R6, R7: 1 kΩ; R0402
RED_LED: LEDCHIPLED_0603; CHIPLED_0603
YELLOW_LED: LEDCHIPLED_0603; CHIPLED_0603

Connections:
BLUE_LED: BLUE_LED.A; also elsewhere on the board
GND: R4.2, R5.2, R6.2, R7.2; also elsewhere on the board
GREEN_LED: GREEN_LED.A; also elsewhere on the board
unnamed: R4.1, RED_LED.C
unnamed: GREEN_LED.C, R5.1
unnamed: BLUE_LED.C, R6.1
unnamed: R7.1, YELLOW_LED.C
RED_LED: RED_LED.A; also elsewhere on the board
YELLOW_LED: YELLOW_LED.A; also elsewhere on the board



Board: 4 copper layers, 29.3 x 15.0 mm, 61 parts (39 on the bottom side), 46 nets.

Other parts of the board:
U$52, U$57: M2_HOLE_PLASTIC

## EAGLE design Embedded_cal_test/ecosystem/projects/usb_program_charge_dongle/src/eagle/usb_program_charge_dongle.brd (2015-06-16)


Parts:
+5V: SMD2; SMD1,27-2,54
BOOT0: SMD2; SMD1,27-2,54
SW2: B3U
USB_D+: SMD2; SMD1,27-2,54
USB_D-: SMD2; SMD1,27-2,54
USB_GND: SMD2; SMD1,27-2,54
V_BATT: SMD2; SMD1,27-2,54

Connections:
+5V: +5V.1, SW2.P$2; also elsewhere on the board
BOOT0: BOOT0.1, SW2.P$1
GND: USB_GND.1; also elsewhere on the board
USB_D+: USB_D+.1; also elsewhere on the board
USB_D-: USB_D-.1; also elsewhere on the board
V_BATT: V_BATT.1; also elsewhere on the board


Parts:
C2: 100 nF; C0603
C3: 4.7 µF; C0603
D_OV_1: PMEG2005EJ,115; SOD323-W
FPF2123: FPF2123; SOT23-5L
R4: 1 MΩ; R0603
R6: 680 Ω; R0603

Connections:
+5V: C2.1, D_OV_1.C; also elsewhere on the board
GND: C2.2, C3.2, FPF2123.2 (GND), R4.1, R6.1; also elsewhere on the board
LOAD_ISET_1: FPF2123.4 (ISET), R6.2
unnamed: D_OV_1.A, FPF2123.5 (VOUT), R4.2
USB_VBUS: C3.1, FPF2123.1 (VIN), FPF2123.3 (ON); also elsewhere on the board


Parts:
C_USB_DC1: 1 µF; C0603
R1, R3: 22 Ω; R0603
R2: 1.5 kΩ; R0603
X1: USB-MICROB

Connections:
D+_IN_1: R1.1, R2.2, X1.D+
D-_IN_1: R3.1, X1.D-
GND: C_USB_DC1.2, X1.GND, X1.MT1 (GND), X1.MT2 (GND); also elsewhere on the board
USB_D+: R1.2; also elsewhere on the board
USB_D-: R3.2; also elsewhere on the board
USB_VBUS: C_USB_DC1.1, R2.1, X1.VBUS; also elsewhere on the board

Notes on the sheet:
As per USB spec, the capacitance across the USB power lines must be between 1µf and 10µf.
Use 5V_USB service and a load limiter like the FPF2123 if your board does not meet this specification or if you are unsure.


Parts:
C1, C4: 1 µF; C0603
U$7: MCP73811; SOT23-5

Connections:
+5V: C1.1, U$7.1 (CE), U$7.4 (VDD), U$7.5 (PROG); also elsewhere on the board
GND: C1.2, C4.2, U$7.2 (VSS); also elsewhere on the board
V_BATT: C4.1, U$7.3 (VBAT); also elsewhere on the board



Board: 2 copper layers, 25.0 x 13.0 mm, 21 parts (5 on the bottom side), 11 nets.

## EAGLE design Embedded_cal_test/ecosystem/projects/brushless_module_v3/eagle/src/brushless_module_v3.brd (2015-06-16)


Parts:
C_MC_VDDA_2: 100nF; C0402
C_MC_VDD_1_2: 10µF; C0402
C_MC_VDD_2_2, C_MC_VDD_3_1: 100nF; C0402
LED1: WHITE; 0402
LED2: GREEN; 0402
LED3: YELLOW; 0402
LED4: RED; 0402
R_BOOT_PD_2: 1kΩ; R0402
R_LED_1, R_LED_2, R_LED_3, R_LED_4: 1kΩ; R0402
R_V_SENSE_1_2: 88.7kΩ; R0402
R_V_SENSE_2_2: 20kΩ; R0402
SW2: B3U
U$14: STM32F303CX; LQFP48

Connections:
16MHZ_CMOS,+,1: U$14.5 (PF0-OSC_IN); also elsewhere on the board
+3V3: C_MC_VDDA_2.1, C_MC_VDD_1_2.1, C_MC_VDD_2_2.1, C_MC_VDD_3_1.1, SW2.P$2, U$14.1 (VBAT), U$14.9 (VDDA/VREF+), U$14.24 (VDD_2), U$14.36 (VDD_3), U$14.48 (VDD_1); also elsewhere on the board
BOOT0_2: R_BOOT_PD_2.1, SW2.P$1, U$14.44 (BOOT0)
CAN_RX_1: U$14.45 (PB8); also elsewhere on the board
CAN_TX_1: U$14.46 (PB9); also elsewhere on the board
CS_OUT_4: U$14.18 (PB0); also elsewhere on the board
D+1: U$14.33 (PA12); also elsewhere on the board
D-1: U$14.32 (PA11); also elsewhere on the board
GND: C_MC_VDDA_2.2, C_MC_VDD_1_2.2, C_MC_VDD_2_2.2, C_MC_VDD_3_1.2, LED1.CATHODE (C), LED2.CATHODE (C), LED3.CATHODE (C), LED4.CATHODE (C), R_BOOT_PD_2.2, R_V_SENSE_2_2.1, U$14.8 (VSSA/VREF-), U$14.23 (VSS_2), U$14.35 (VSS_3), U$14.47 (VSS_1); also elsewhere on the board
INDEX1: U$14.41 (PB5); also elsewhere on the board
LED_1: R_LED_1.2, U$14.2 (PC13)
LED_2: R_LED_2.2, U$14.3 (PC14-OSC32_IN)
LED_3: R_LED_3.2, U$14.4 (PC15-OSC32_OUT)
LED_4: R_LED_4.2, U$14.6 (PF1-OSC_OUT)
MBUS_SCL_1: U$14.38 (PA15); also elsewhere on the board
MBUS_SDA_1: U$14.37 (PA14); also elsewhere on the board
unnamed: LED4.ANODE (A), R_LED_4.1
unnamed: LED3.ANODE (A), R_LED_3.1
unnamed: LED2.ANODE (A), R_LED_2.1
unnamed: LED1.ANODE (A), R_LED_1.1
POS_PWM1: U$14.39 (PB3); also elsewhere on the board
PWM_H_1: U$14.29 (PA8); also elsewhere on the board
PWM_H_2: U$14.30 (PA9); also elsewhere on the board
PWM_H_3: U$14.31 (PA10); also elsewhere on the board
PWM_L_1: U$14.26 (PB13); also elsewhere on the board
PWM_L_2: U$14.27 (PB14); also elsewhere on the board
PWM_L_3: U$14.28 (PB15); also elsewhere on the board
QEPA1: U$14.42 (PB6); also elsewhere on the board
QEPB1: U$14.43 (PB7); also elsewhere on the board
VS_OUT: R_V_SENSE_1_2.1, R_V_SENSE_2_2.2, U$14.19 (PB1)
V_BATT: R_V_SENSE_1_2.2; also elsewhere on the board

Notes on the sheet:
If using A2D

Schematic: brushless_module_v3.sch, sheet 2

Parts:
C_DC_ENC1_1: 10µF; C0402
C_DC_ENC2_1: 100nF; C0402
ENC1: AS5040; SSOP16
LED_MAG_G1: GREEN; 0402
LED_MAG_Y1: YELLOW; 0402
LED_POS1: BLUE; 0402
R_MAG_G1: 1kΩ; R0402
R_MAG_Y1: 1kΩ; R0402
R_POS1: 1kΩ; R0402

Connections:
+3V3: C_DC_ENC2_1.1, ENC1.16 (VDD5V), R_MAG_G1.2, R_MAG_Y1.2; also elsewhere on the board
ENC_3V3_1: C_DC_ENC1_1.1, ENC1.15 (VDD3V3)
GND: C_DC_ENC1_1.2, C_DC_ENC2_1.2, ENC1.7 (VSS), ENC1.8 (PROG), ENC1.11 (CSN), LED_MAG_G1.CATHODE (C), LED_MAG_Y1.CATHODE (C), R_POS1.1; also elsewhere on the board
INDEX1: ENC1.6 (INDEX_W); also elsewhere on the board
MAGDEC1: ENC1.2 (MAGDEC), LED_MAG_Y1.ANODE (A), R_MAG_Y1.1
MAGINC1: ENC1.1 (MAGINC), LED_MAG_G1.ANODE (A), R_MAG_G1.1
unnamed: LED_POS1.ANODE (A), R_POS1.2
POS_PWM1: ENC1.12 (PWN), LED_POS1.CATHODE (C); also elsewhere on the board
QEPA1: ENC1.3 (A_LSB_U); also elsewhere on the board
QEPB1: ENC1.4 (B_DIR_V); also elsewhere on the board

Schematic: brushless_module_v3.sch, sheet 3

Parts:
CS_4: INA21X; SC70
C_CS_DC_4: 100nF; C0402
C_S_1: 10µF; C0402
R_CS_4: 1mΩ; R1206
R_CS_REF1_4, R_CS_REF2_4: 10kΩ; R0402
R_S1_1, R_S2_1: 10Ω; R0402

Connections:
+3V3: R_CS_REF1_4.2; also elsewhere on the board
CS_OUT_4: CS_4.P6 (OUT); also elsewhere on the board
GND: CS_4.P2 (GND), C_CS_DC_4.2, R_CS_REF2_4.1; also elsewhere on the board
IN+_1: CS_4.P4 (IN+), C_S_1.1, R_S2_1.1
IN-_1: CS_4.P5 (IN-), C_S_1.2, R_S1_1.1
V+: R_CS_4.1, R_S1_1.2; also elsewhere on the board
V_BATT: CS_4.P3 (V+), C_CS_DC_4.1, R_CS_4.2, R_S2_1.2; also elsewhere on the board
V_REF_CS: CS_4.P1 (REF), R_CS_REF1_4.1, R_CS_REF2_4.2

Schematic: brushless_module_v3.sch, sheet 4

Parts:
C3: 10µF; C0402
D_OV_1: PMEG2005EJ,115; SOD323-W
FPF2123: FPF2123; SOT23-5L
R4: 1MΩ; R0402
R6: 604Ω; R0402

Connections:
+5V: C3.1, FPF2123.1 (VIN), FPF2123.3 (ON); also elsewhere on the board
GND: C3.2, FPF2123.2 (GND), R4.1, R6.1; also elsewhere on the board
LOAD_ISET_1: FPF2123.4 (ISET), R6.2
unnamed: D_OV_1.A, FPF2123.5 (VOUT), R4.2
V_BATT: D_OV_1.C; also elsewhere on the board

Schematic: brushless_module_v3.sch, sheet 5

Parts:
R11, R12: 1kΩ; R0402
U$57: SM06B-SRSS-TB

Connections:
+3V3: R11.2, R12.2, U$57.P$3 (3); also elsewhere on the board
CAN_H_1: U$57.P$6 (6); also elsewhere on the board
CAN_L_1: U$57.P$5 (5); also elsewhere on the board
GND: U$57.P$1 (1); also elsewhere on the board
MBUS_SCL_1: R12.1, U$57.P$2 (2); also elsewhere on the board
MBUS_SDA_1: R11.1, U$57.P$4 (4); also elsewhere on the board

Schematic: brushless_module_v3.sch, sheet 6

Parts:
U$9: DEANS-MICRO-3PIN

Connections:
INV_OUT1: U$9.P$1 (1); also elsewhere on the board
INV_OUT2: U$9.P$3 (3); also elsewhere on the board
INV_OUT3: U$9.P$2 (2); also elsewhere on the board

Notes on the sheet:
Done with vias because no pinhead was proper size

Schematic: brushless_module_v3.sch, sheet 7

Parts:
C6: 100nF; C0402
U$54: ASTX-H11

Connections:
16MHZ_CMOS,+,1: U$54.P$3 (OUT); also elsewhere on the board
+3V3: C6.1, U$54.P$4 (VDD); also elsewhere on the board
GND: C6.2, U$54.P$2 (GND); also elsewhere on the board

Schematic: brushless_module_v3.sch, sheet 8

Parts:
CIN_1: 10µF; C0603
COUT_1: 22µF; C0603
D_UV_2: PMEG2005EJ,115; SOD323-W
L1: 2.2µH; L2012C
MMSZ4684T1G1: D-SOD123; SOD123
U$37: TPS621XX; 8-WFDFN

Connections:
+3V3: COUT_1.1, L1.2, MMSZ4684T1G1.1 (C), U$37.P$6 (VOS); also elsewhere on the board
GND: CIN_1.2, COUT_1.2, D_UV_2.A, MMSZ4684T1G1.2 (A), U$37.P$1 (PGND), U$37.P$4 (AGND), U$37.P$5 (FB), U$37.P$9 (AGND); also elsewhere on the board
GPIO,#,+,O: U$37.P$8 (PG)
unnamed: L1.1, U$37.P$7 (SW)
V+: CIN_1.1, D_UV_2.C, U$37.P$2 (VIN), U$37.P$3 (EN); also elsewhere on the board

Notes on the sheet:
The GPIO is an open drain and requires a pull up or a micro's internal pull up

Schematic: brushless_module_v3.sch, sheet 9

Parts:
R5: 1.5kΩ; R0402
R7, R8: 22Ω; R0402
X1: USB-MICROB

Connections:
+5V: R5.1, X1.VBUS; also elsewhere on the board
D+1: R7.2; also elsewhere on the board
D+_IN_2: R5.2, R7.1, X1.D+
D-1: R8.2; also elsewhere on the board
D-_IN_2: R8.1, X1.D-
GND: X1.GND, X1.MT1 (GND), X1.MT2 (GND); also elsewhere on the board

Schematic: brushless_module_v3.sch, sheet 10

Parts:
CAN_TRAN1: MAX3051; SOT23-8L
C_CAN_DC1: 100nF; C0402
R_RS1: 10kΩ; R0402

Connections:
+3V3: CAN_TRAN1.3 (VCC), C_CAN_DC1.1; also elsewhere on the board
CAN_H_1: CAN_TRAN1.7 (CANH); also elsewhere on the board
CAN_L_1: CAN_TRAN1.6 (CANL); also elsewhere on the board
CAN_RX_1: CAN_TRAN1.4 (RXD); also elsewhere on the board
CAN_TX_1: CAN_TRAN1.1 (TXD); also elsewhere on the board
GND: CAN_TRAN1.2 (GND), CAN_TRAN1.5 (SHDN), C_CAN_DC1.2, R_RS1.1; also elsewhere on the board
unnamed: CAN_TRAN1.8 (RS), R_RS1.2

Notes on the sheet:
Optional
R_RS (kΩ) = 12000 / (maximum speed in kbps)

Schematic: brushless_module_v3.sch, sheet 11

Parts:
C1: 47µF; C1206
D_FLYBACK1_1, D_FLYBACK2_1: BAS 52-02V H6327; SOD523
R_SLEW_H_1: 1Ω; R0402
R_SLEW_L_1: 1Ω; R0402
U$62: SI7139DP-T1-GE3; S0-8-POWERPAK
U$63: SIR466DP-T1-GE3; S0-8-POWERPAK
U$64: UCC2752XUCC27524DSD; 8-WDFN

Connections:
DRIVER_OUT_H_1: R_SLEW_H_1.1, U$64.P5 (OUTB)
DRIVER_OUT_L_1: R_SLEW_L_1.1, U$64.P7 (OUTA)
GATE_H_1: R_SLEW_H_1.2, U$62.4 (G)
GATE_L_1: R_SLEW_L_1.2, U$63.4 (G)
GND: C1.2, D_FLYBACK2_1.A, U$63.1 (S), U$63.2 (S), U$63.3 (S), U$64.EP (GND), U$64.P3 (GND); also elsewhere on the board
INV_OUT1: D_FLYBACK1_1.A, D_FLYBACK2_1.C, U$62.5 (D), U$62.6 (D), U$62.7 (D), U$62.8 (D), U$62.P$1 (D), U$63.5 (D), U$63.6 (D), U$63.7 (D), U$63.8 (D), U$63.P$1 (D); also elsewhere on the board
PWM_H_1: U$64.P2 (INA); also elsewhere on the board
PWM_L_1: U$64.P4 (INB); also elsewhere on the board
V+: C1.1, D_FLYBACK1_1.C, U$62.1 (S), U$62.2 (S), U$62.3 (S), U$64.P6 (VDD); also elsewhere on the board

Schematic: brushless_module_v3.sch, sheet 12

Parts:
C4: 47µF; C1206
D_FLYBACK1_2, D_FLYBACK2_2: BAS 52-02V H6327; SOD523
R_SLEW_H_2: 1Ω; R0402
R_SLEW_L_2: 1Ω; R0402
U$71: SI7139DP-T1-GE3; S0-8-POWERPAK
U$72: SIR466DP-T1-GE3; S0-8-POWERPAK
U$73: UCC2752XUCC27524DSD; 8-WDFN

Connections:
DRIVER_OUT_H_2: R_SLEW_H_2.1, U$73.P7 (OUTA)
DRIVER_OUT_L_2: R_SLEW_L_2.1, U$73.P5 (OUTB)
GATE_H_2: R_SLEW_H_2.2, U$71.4 (G)
GATE_L_2: R_SLEW_L_2.2, U$72.4 (G)
GND: C4.2, D_FLYBACK2_2.A, U$72.1 (S), U$72.2 (S), U$72.3 (S), U$73.EP (GND), U$73.P3 (GND); also elsewhere on the board
INV_OUT2: D_FLYBACK1_2.A, D_FLYBACK2_2.C, U$71.5 (D), U$71.6 (D), U$71.7 (D), U$71.8 (D), U$71.P$1 (D), U$72.5 (D), U$72.6 (D), U$72.7 (D), U$72.8 (D), U$72.P$1 (D); also elsewhere on the board
PWM_H_2: U$73.P2 (INA); also elsewhere on the board
PWM_L_2: U$73.P4 (INB); also elsewhere on the board
V+: C4.1, D_FLYBACK1_2.C, U$71.1 (S), U$71.2 (S), U$71.3 (S), U$73.P6 (VDD); also elsewhere on the board

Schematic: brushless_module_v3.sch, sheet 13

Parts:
C5: 47µF; C1206
D_FLYBACK1_3, D_FLYBACK2_3: BAS 52-02V H6327; SOD523
R_SLEW_H_3: 1Ω; R0402
R_SLEW_L_3: 1Ω; R0402
U$80: SI7139DP-T1-GE3; S0-8-POWERPAK
U$81: SIR466DP-T1-GE3; S0-8-POWERPAK
U$82: UCC2752XUCC27524DSD; 8-WDFN

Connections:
DRIVER_OUT_H_3: R_SLEW_H_3.1, U$82.P5 (OUTB)
DRIVER_OUT_L_3: R_SLEW_L_3.1, U$82.P7 (OUTA)
GATE_H_3: R_SLEW_H_3.2, U$80.4 (G)
GATE_L_3: R_SLEW_L_3.2, U$81.4 (G)
GND: C5.2, D_FLYBACK2_3.A, U$81.1 (S), U$81.2 (S), U$81.3 (S), U$82.EP (GND), U$82.P3 (GND); also elsewhere on the board
INV_OUT3: D_FLYBACK1_3.A, D_FLYBACK2_3.C, U$80.5 (D), U$80.6 (D), U$80.7 (D), U$80.8 (D), U$80.P$1 (D), U$81.5 (D), U$81.6 (D), U$81.7 (D), U$81.8 (D), U$81.P$1 (D); also elsewhere on the board
PWM_H_3: U$82.P2 (INA); also elsewhere on the board
PWM_L_3: U$82.P4 (INB); also elsewhere on the board
V+: C5.1, D_FLYBACK1_3.C, U$80.1 (S), U$80.2 (S), U$80.3 (S), U$82.P6 (VDD); also elsewhere on the board

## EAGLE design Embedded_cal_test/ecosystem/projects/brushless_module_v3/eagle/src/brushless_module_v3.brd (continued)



Board: 4 copper layers, 30.0 x 30.0 mm, 84 parts (51 on the bottom side), 63 nets.

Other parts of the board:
U$6: MODLAB
U$12: PENN_ENGINEERING

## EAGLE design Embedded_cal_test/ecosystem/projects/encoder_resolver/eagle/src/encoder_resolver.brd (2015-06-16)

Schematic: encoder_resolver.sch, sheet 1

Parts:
C_MC_VDDA_1: 100nF; C0603
C_MC_VDD_1_1: 4.7uF; C0603
C_MC_VDD_2_1: 100nF; C0603
IC7: STM32F373CC; LQFP48
LED1, LED2, LED3, LED4: LEDCHIPLED_0603; CHIPLED_0603
OSC1: FOX924B; 4-SMD_5X3.2
R_BOOT_PU_1: 1k; R0603
R_LED_1, R_LED_3, R_LED_4, R_LED_5: 1k; R0603
R_NRST_PU_1: 1k; R0603
R_V_SENSE_1_1: 88.7kΩ; R0603
R_V_SENSE_2_1: 20kΩ; R0603
SW1: B3U

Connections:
16MHZ_3V3: IC7.5 (PF0-OSC_IN-I2C2SDA+), OSC1.P$3 (OUTPUT)
+3V3: C_MC_VDDA_1.1, C_MC_VDD_1_1.1, C_MC_VDD_2_1.1, IC7.1 (VBAT), IC7.9 (VDDA-VREF+), IC7.17 (VDD_2), IC7.24 (VDDSD), IC7.25 (VREFSD), IC7.48 (VDD_1), LED1.A, LED2.A, LED3.A, LED4.A, OSC1.P$4 (VCC), R_NRST_PU_1.1, SW1.P$2; also elsewhere on the board
BOOT0_1: IC7.44 (BOOT0), R_BOOT_PU_1.1, SW1.P$1
D+1: IC7.33 (PA12-USART1RTS/USBDP/SPI1SCK); also elsewhere on the board
D-1: IC7.32 (PA11-USART1CTS/USBDM/SPI2NSS/SPI1NSS); also elsewhere on the board
ENC_CLK_1: IC7.11 (PA1-USART2RTS/ADC1/SPI3SCK/TIM2CH2); also elsewhere on the board
ENC_CSN_1: IC7.10 (PA0-USART2CTS/ADC0); also elsewhere on the board
ENC_MISO_1: IC7.12 (PA2-USART2TX/ADC2/SPI3MISO/TIM2CH3); also elsewhere on the board
E_R1-R2_MICRO: IC7.16 (PA6-SPI1MISO/ADC6/TIM3CH1); also elsewhere on the board
E_S1-S3_MICRO: IC7.14 (PA4-SPI1NSS/ADC4/SPI3NSS/USART2CK); also elsewhere on the board
E_S2-S4_MICRO: IC7.15 (PA5-SPI1SCK/ADC5); also elsewhere on the board
GND: C_MC_VDDA_1.2, C_MC_VDD_1_1.2, C_MC_VDD_2_1.2, IC7.8 (VSSA-VREF-), IC7.23 (VSSD-VREFSD-), IC7.47 (VSS_1), OSC1.P$2 (GND), R_BOOT_PU_1.2, R_V_SENSE_2_1.1; also elsewhere on the board
INDEX1: IC7.6 (PF1-OSC_OUT-I2C2SCL+); also elsewhere on the board
MAGDEC1: IC7.41 (PB5-SPI1MOSI/SPI3MOSI); also elsewhere on the board
unnamed: LED1.C, R_LED_1.2
unnamed: IC7.18 (PB0-ADC8/SPI1MOSI/TIM3CH3), R_V_SENSE_1_1.1, R_V_SENSE_2_1.2
unnamed: IC7.38 (PA15-I2C1SCL+), R_LED_1.1
unnamed: LED2.C, R_LED_3.2
unnamed: IC7.37 (PA14-I2C1SDA+), R_LED_3.1
unnamed: LED4.C, R_LED_4.2
unnamed: LED3.C, R_LED_5.2
unnamed: IC7.29 (PA8-USART1CK/SPI2SCK/MCO), R_LED_4.1
unnamed: IC7.30 (PA9-USART1TX/SPI2MISO), R_LED_5.1
NRST_1: IC7.7 (NRST), R_NRST_PU_1.2
POS_PWM1: IC7.13 (PA3-USART2RX/ADC3/SPI3MOSI/TIM2CH4); also elsewhere on the board
QEPA1: IC7.42 (PB6-I2C1SCL+); also elsewhere on the board
QEPB1: IC7.43 (PB7-I2C1SDA+); also elsewhere on the board
V+: R_V_SENSE_1_1.2; also elsewhere on the board

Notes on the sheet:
Delete if more than one of this sheet

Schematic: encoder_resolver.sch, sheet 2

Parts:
R1: 22Ω; R0603
R2: 1.5k; R0603
R3: 22; R0603
X1: USB-MICROB

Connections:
+5V/1: R2.1, X1.VBUS; also elsewhere on the board
D+1: R1.2; also elsewhere on the board
D+_IN_1: R1.1, R2.2, X1.D+
D-1: R3.2; also elsewhere on the board
D-_IN_1: R3.1, X1.D-
GND: X1.GND, X1.MT1 (GND), X1.MT2 (GND); also elsewhere on the board

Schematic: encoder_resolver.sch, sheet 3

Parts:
C_DC_ENC1_1: 10uF; C0603
C_DC_ENC2_1: 100nF; C0603
ENC1: AS5040; SSOP16
LED_MAG_G1: G; CHIP-LED0603
LED_POS1: B; CHIP-LED0603
R_MAG_G1: 1kΩ; R0603
R_POS1: 1kΩ; R0603

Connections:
+3V3: C_DC_ENC2_1.1, ENC1.16 (VDD5V), R_MAG_G1.2; also elsewhere on the board
ENC_3V3_1: C_DC_ENC1_1.1, ENC1.15 (VDD3V3)
ENC_CLK_1: ENC1.10 (CLK); also elsewhere on the board
ENC_CSN_1: ENC1.11 (CSN); also elsewhere on the board
ENC_MISO_1: ENC1.9 (D0); also elsewhere on the board
GND: C_DC_ENC1_1.2, C_DC_ENC2_1.2, ENC1.7 (VSS), ENC1.8 (PROG), LED_MAG_G1.C, LED_POS1.C; also elsewhere on the board
INDEX1: ENC1.6 (INDEX_W); also elsewhere on the board
MAGDEC1: ENC1.2 (MAGDEC); also elsewhere on the board
MAGINC1: ENC1.1 (MAGINC), LED_MAG_G1.A, R_MAG_G1.1
unnamed: LED_POS1.A, R_POS1.2
POS_PWM1: ENC1.12 (PWN), R_POS1.1; also elsewhere on the board
QEPA1: ENC1.3 (A_LSB_U); also elsewhere on the board
QEPB1: ENC1.4 (B_DIR_V); also elsewhere on the board

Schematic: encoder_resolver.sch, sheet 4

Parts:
CIN1_1, CIN2_1: 10µF; C0805
COUT1_1, COUT2_1: 22µF; C0603
C_BOOST1: 22nF; C0603
L_REG1: 4.7µH; VLC5045
SW_REG1: MCP16323; QFN16

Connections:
+5V: COUT1_1.1, COUT2_1.1, L_REG1.2, SW_REG1.5 (VFB); also elsewhere on the board
BOOST1: C_BOOST1.1, SW_REG1.10 (BOOST)
GND: CIN1_1.2, CIN2_1.2, COUT1_1.2, COUT2_1.2, SW_REG1.4 (SGND), SW_REG1.14 (PGND), SW_REG1.15 (PGND), SW_REG1.TH (SGND); also elsewhere on the board
SW1: C_BOOST1.2, L_REG1.1, SW_REG1.1 (SW), SW_REG1.12 (SW), SW_REG1.13 (SW), SW_REG1.16 (SW)
V+: CIN1_1.1, CIN2_1.1, SW_REG1.2 (VIN), SW_REG1.3 (VIN), SW_REG1.11 (VIN); also elsewhere on the board

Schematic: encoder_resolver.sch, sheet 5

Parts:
C_BYP_IN_1: 10µF; C1206
C_BYP_OUT_1: 10µF; C0603
U$6: LD111733; SOT-223

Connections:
+3V3: C_BYP_OUT_1.1, U$6.2 (VOUT), U$6.4 (VOUT); also elsewhere on the board
+5V: C_BYP_IN_1.1, U$6.3 (VIN); also elsewhere on the board
GND: C_BYP_IN_1.2, C_BYP_OUT_1.2, U$6.1 (GND); also elsewhere on the board

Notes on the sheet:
Default is +3V3, change here!

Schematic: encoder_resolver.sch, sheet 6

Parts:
C2: 100nF; C0603
C3: 10uF; C0603
D_OV_1: PMEG2005EJ,115; SOD323-W
FPF: FPF; SOT23-5L
R4: 1MΩ; R0603
R6: 604Ω; R0603

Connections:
+5V: C2.1, D_OV_1.C; also elsewhere on the board
+5V/1: C3.1, FPF.1 (VIN), FPF.3 (ON); also elsewhere on the board
GND: C2.2, C3.2, FPF.2 (GND), R4.1, R6.1; also elsewhere on the board
LOAD_ISET_1: FPF.4 (ISET), R6.2
unnamed: D_OV_1.A, FPF.5 (VOUT), R4.2

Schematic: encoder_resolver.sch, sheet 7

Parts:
JP1: PINHD-1X6; 1X06
P_POWER: PINHD-1X2; 1X02

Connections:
E_R1: JP1.1; also elsewhere on the board
E_R2: JP1.2; also elsewhere on the board
E_S1: JP1.5; also elsewhere on the board
E_S2: JP1.3; also elsewhere on the board
E_S3: JP1.6; also elsewhere on the board
E_S4: JP1.4; also elsewhere on the board
GND: P_POWER.2; also elsewhere on the board
V+: P_POWER.1; also elsewhere on the board

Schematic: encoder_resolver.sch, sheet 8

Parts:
C1, C4, C7, C8, C10, C11: 1µF; C0603
C5: 1nF; C0603
C6, C9: 100pF; C0603
IC1: AD8544RU; TSSOP14
R5, R11: 100kΩ; R0603
R7, R8, R15, R17, R19, R21: 10kΩ; R0603
R9: 4.7kΩ; R0603
R10, R14, R18, R22: 1kΩ; R0603
R12, R13: 22kΩ; R0603
R16, R20: 12.7kΩ; R0603

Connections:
+3V3: R7.2; also elsewhere on the board
E_R1: C1.1; also elsewhere on the board
E_R1-R2_MICRO: C5.1, R14.1; also elsewhere on the board
E_R2: C4.1; also elsewhere on the board
E_S1: C10.1, R22.1; also elsewhere on the board
E_S1-S3_MICRO: R19.2; also elsewhere on the board
E_S2: C7.1, R18.1; also elsewhere on the board
E_S2-S4_MICRO: R15.2; also elsewhere on the board
E_S3: C11.1, R22.2; also elsewhere on the board
E_S4: C8.1, R18.2; also elsewhere on the board
GND: C5.2, C6.2, C8.2, C9.2, C11.2, IC1.11 (V-), R8.1, R17.1, R21.1; also elsewhere on the board
unnamed: IC1.3 (IN+), R7.1, R8.2
unnamed: IC1.2 (IN-), R9.2
unnamed: C4.2, R5.1, R10.2
unnamed: C1.2, R10.1, R11.1
unnamed: IC1.5 (IN+), R5.2, R13.2
unnamed: IC1.6 (IN-), R11.2, R12.1
unnamed: IC1.7 (OUT), R12.2, R14.2
unnamed: C6.1, IC1.10 (IN+), R15.1
unnamed: IC1.9 (IN-), R16.1, R17.2
unnamed: C7.2, IC1.8 (OUT), R16.2
unnamed: C9.1, IC1.12 (IN+), R19.1
unnamed: IC1.13 (IN-), R20.1, R21.2
unnamed: C10.2, IC1.14 (OUT), R20.2
V+: IC1.4 (V+); also elsewhere on the board
VCC/2: IC1.1 (OUT), R9.1, R13.1



Board: 2 copper layers, 44.0 x 43.0 mm, 75 parts (58 on the bottom side), 59 nets.

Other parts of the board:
U$11: PENN_ENGINEERING

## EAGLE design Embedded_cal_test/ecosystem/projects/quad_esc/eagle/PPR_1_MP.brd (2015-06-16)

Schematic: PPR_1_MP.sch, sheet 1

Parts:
C_MC_VDDA_1: 100nF; C0402
C_MC_VDD_1_1: 4.7uF; C0402
C_MC_VDD_2_1: 100nF; C0402
C_NRST_LP_1: 4.7uF; C0603K
IC5: SN74LVC2G14DCKR; DCK
IC6: SN74LVC1G373DCKR; DCK
IC7: STM32F373CC; LQFP48
LED_RST_1: orange; CHIPLED_0603
LED_RST_4: white; CHIPLED_0603
LED_STAT_1: red; CHIPLED_0603
LED_STAT_2: green; CHIPLED_0603
LED_STAT_3: blue; CHIPLED_0603
OSC1: FOX924B; 4-SMD_5X3.2
R_NRST_LP_1: 220k; R0402
R_NRST_PU_1: 1k; R0402
R_RST_LED_1: 1k; R0402
R_STAT_LED_1, R_STAT_LED_2, R_STAT_LED_3, R_STAT_LED_4: 1k; R0402
SW1: B3U

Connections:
16MHZ_3V3: IC7.5 (PF0-OSC_IN-I2C2SDA+), OSC1.P$3 (OUTPUT); also elsewhere on the board
+3V3: C_MC_VDDA_1.1, C_MC_VDD_1_1.1, C_MC_VDD_2_1.1, IC5.P$5 (V+), IC6.P$5 (V+), IC7.1 (VBAT), IC7.9 (VDDA-VREF+), IC7.17 (VDD_2), IC7.24 (VDDSD), IC7.25 (VREFSD), IC7.48 (VDD_1), OSC1.P$4 (VCC), R_NRST_PU_1.1; also elsewhere on the board
BOOT0_1: IC5.P$6 (1Y), IC6.P$3 (D), IC7.44 (BOOT0)
D+1: IC7.33 (PA12-USART1RTS/USBDP/SPI1SCK); also elsewhere on the board
D-1: IC7.32 (PA11-USART1CTS/USBDM/SPI2NSS/SPI1NSS); also elsewhere on the board
GND: C_MC_VDDA_1.2, C_MC_VDD_1_1.2, C_MC_VDD_2_1.2, C_NRST_LP_1.2, IC5.P$2 (GND), IC6.P$2 (GND), IC6.P$6 (_OE), IC7.8 (VSSA-VREF-), IC7.23 (VSSD-VREFSD-), IC7.47 (VSS_1), OSC1.P$2 (GND), R_RST_LED_1.1, R_STAT_LED_1.1, R_STAT_LED_2.1, R_STAT_LED_3.1, R_STAT_LED_4.1, SW1.P$1; also elsewhere on the board
IMU_SCL_1: IC7.38 (PA15-I2C1SCL+); also elsewhere on the board
IMU_SDA_1: IC7.37 (PA14-I2C1SDA+); also elsewhere on the board
LED_RST_1_1: IC6.P$4 (Q), LED_RST_1.A
LED_RST_2_1: LED_RST_1.C, R_RST_LED_1.2
LED_RST_2_2: LED_STAT_1.C, R_STAT_LED_1.2
LED_RST_2_3: LED_STAT_2.C, R_STAT_LED_2.2
LED_RST_2_5: LED_RST_4.C, R_STAT_LED_4.2
LED_STAT_2_3: LED_STAT_3.C, R_STAT_LED_3.2
LE_1: IC5.P$4 (2Y), IC6.P$1 (LE)
unnamed: IC7.20 (PB2), LED_STAT_3.A
unnamed: IC7.18 (PB0-ADC8/SPI1MOSI/TIM3CH3), LED_STAT_1.A
unnamed: IC7.19 (PB1-ADC9/TIM3CH4), LED_STAT_2.A
unnamed: IC7.21 (PE8), LED_RST_4.A
NRST_1: IC5.P$3 (2A), IC7.7 (NRST), R_NRST_LP_1.2, R_NRST_PU_1.2, SW1.P$2
NRST_LP_1: C_NRST_LP_1.1, IC5.P$1 (1A), R_NRST_LP_1.1
PWM_1: IC7.40 (PB4-SPI1MISO/SPI3MISO); also elsewhere on the board
PWM_2: IC7.41 (PB5-SPI1MOSI/SPI3MOSI); also elsewhere on the board
PWM_3: IC7.42 (PB6-I2C1SCL+); also elsewhere on the board
PWM_4: IC7.43 (PB7-I2C1SDA+); also elsewhere on the board
ZB_IRQ_1: IC7.22 (PE9); also elsewhere on the board
ZB_MISO_1: IC7.26 (PB14-SPI2MISO); also elsewhere on the board
ZB_MOSI_1: IC7.27 (PB15-SPI2MOSI); also elsewhere on the board
ZB_SCLK_1: IC7.28 (PD8-SPI2SCK); also elsewhere on the board

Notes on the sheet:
Latch D > Q
Inverter (not gate)
Push reset, hold boot
Delete if more than one of this sheet
If using A2D

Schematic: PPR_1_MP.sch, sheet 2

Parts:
BALUN1: 0896FB15A0100
CB1, CB2, CB3, CB4: 1µF; C0603
C_RF_CU1_1, C_RF_CU2_1: 68µF; C0603
C_ZB_XTRF1: 100nF; C0603
JP1: Whip; 1X01M
RADIO1: AT86RF; QFNN32
R_CLK_VDIV1_1: 5k6; R0603
R_CLK_VDIV2_1: 1k; R0603

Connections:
16MHZ_0V5_1: C_ZB_XTRF1.2, R_CLK_VDIV1_1.1, R_CLK_VDIV2_1.2
16MHZ_0V5_AC1: C_ZB_XTRF1.1, RADIO1.26 (XTAL1)
16MHZ_3V3: R_CLK_VDIV1_1.2; also elsewhere on the board
+3V3: CB2.1, CB4.1, RADIO1.15 (DEVDD), RADIO1.28 (EVDD); also elsewhere on the board
ANT1: BALUN1.1 (UNBALANCED), JP1.1
GND: BALUN1.2 (GND), BALUN1.5 (GND), BALUN1.6 (GND), CB1.2, CB2.2, CB3.2, CB4.2, RADIO1.3 (AVSS), RADIO1.6 (AVSS), RADIO1.7 (DVSS), RADIO1.12 (DVSS), RADIO1.16 (DVSS), RADIO1.18 (DVSS), RADIO1.21 (DVSS), RADIO1.23 (\SEL), RADIO1.27 (AVSS), RADIO1.30 (AVSS), RADIO1.31 (AVSS), RADIO1.32 (AVSS), RADIO1.EXP (AVSS), R_CLK_VDIV2_1.1; also elsewhere on the board
ZB_AVDD1: CB1.1, RADIO1.29 (AVDD)
ZB_BAL1_1: BALUN1.3 (BALANCED1), C_RF_CU1_1.2
ZB_BAL2_1: BALUN1.4 (BALANCED2), C_RF_CU2_1.2
ZB_DVDD1: CB3.1, RADIO1.13 (DVDD), RADIO1.14 (DVDD)
ZB_IRQ_1: RADIO1.24 (IRQ); also elsewhere on the board
ZB_MISO_1: RADIO1.20 (MISO); also elsewhere on the board
ZB_MOSI_1: RADIO1.22 (MOSI); also elsewhere on the board
ZB_RFN1: C_RF_CU2_1.1, RADIO1.4 (RFP)
ZB_RFP1: C_RF_CU1_1.1, RADIO1.5 (RFN)
ZB_SCLK_1: RADIO1.19 (SCLK); also elsewhere on the board

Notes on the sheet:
Connect ZB_SEL_x to the cable select pin
Connect ZB_MOSI_x to MOSI RPx pin
Connect ZB_SCLK_x to the SPI clock PRx pin
Connect ZB_MISO_x to MISO PRIx pin
Connect ZB_IRQ_x to the Interrupt Request pin
Equal length, short
Short

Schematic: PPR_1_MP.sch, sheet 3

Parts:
CN2: FCI-10103594-0001LF
R1, R3: 22Ω; R0402
R2: 1.5k; R0402

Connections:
D+1: R1.2; also elsewhere on the board
D+_IN_1: CN2.3 (D+), R1.1, R2.2
D-1: R3.2; also elsewhere on the board
D-_IN_1: CN2.2 (D-), R3.1
GND: CN2.5 (GND); also elsewhere on the board
V+: CN2.1 (VCC), R2.1; also elsewhere on the board

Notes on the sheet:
Connect VBUSx to the VBUS pin on the microcontroller
Connect D+x to the D+ pin on the microcontroller
Connect D-x to the D- pin on the microcontroller
The maximum capacitance on VBUS is 10µF and minimum is 1µF
IF DRAWING POWER FROM USB, CHECK THE VOLTAGE REGULATOR FOR CAPACITANCE

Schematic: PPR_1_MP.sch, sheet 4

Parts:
JP11: PINHD-1X2; 1X02
Q1: ZXMN3A01F; SOT23-3
R_LIM_1: 330Ω; R0805

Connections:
DRIVER_OUT_1: JP11.2, Q1.3 (D)
GATE_1: Q1.1 (G), R_LIM_1.2
GND: Q1.2 (S); also elsewhere on the board
PWM_1: R_LIM_1.1; also elsewhere on the board
V+: JP11.1; also elsewhere on the board

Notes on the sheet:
Connect PWM_x to the PWMxx microcontroller pin
Connect DRIVER_OUT_X to the load

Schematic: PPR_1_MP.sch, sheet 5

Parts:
JP2: PINHD-1X2; 1X02
Q2: ZXMN3A01F; SOT23-3
R_LIM_2: 330Ω; R0805

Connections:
DRIVER_OUT_2: JP2.2, Q2.3 (D)
GATE_2: Q2.1 (G), R_LIM_2.2
GND: Q2.2 (S); also elsewhere on the board
PWM_2: R_LIM_2.1; also elsewhere on the board
V+: JP2.1; also elsewhere on the board

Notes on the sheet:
Connect PWM_x to the PWMxx microcontroller pin
Connect DRIVER_OUT_X to the load

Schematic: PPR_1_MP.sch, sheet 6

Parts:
JP3: PINHD-1X2; 1X02
Q3: ZXMN3A01F; SOT23-3
R_LIM_3: 330Ω; R0805

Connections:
DRIVER_OUT_3: JP3.2, Q3.3 (D)
GATE_3: Q3.1 (G), R_LIM_3.2
GND: Q3.2 (S); also elsewhere on the board
PWM_3: R_LIM_3.1; also elsewhere on the board
V+: JP3.1; also elsewhere on the board

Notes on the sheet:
Connect PWM_x to the PWMxx microcontroller pin
Connect DRIVER_OUT_X to the load

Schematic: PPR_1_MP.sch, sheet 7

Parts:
JP4: PINHD-1X2; 1X02
Q4: ZXMN3A01F; SOT23-3
R_LIM_4: 330Ω; R0805

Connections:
DRIVER_OUT_4: JP4.2, Q4.3 (D)
GATE_4: Q4.1 (G), R_LIM_4.2
GND: Q4.2 (S); also elsewhere on the board
PWM_4: R_LIM_4.1; also elsewhere on the board
V+: JP4.1; also elsewhere on the board

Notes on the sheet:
Connect PWM_x to the PWMxx microcontroller pin
Connect DRIVER_OUT_X to the load

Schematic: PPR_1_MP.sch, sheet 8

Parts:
C_BYP_IN_1: 10µF; C1206
C_BYP_OUT_1: 10µF; C0603
REG: LD1117XX; SOT-223

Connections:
+3V3: C_BYP_OUT_1.1, REG.2 (VOUT), REG.4 (VOUT2); also elsewhere on the board
GND: C_BYP_IN_1.2, C_BYP_OUT_1.2, REG.1 (GND); also elsewhere on the board
V+: C_BYP_IN_1.1, REG.3 (VIN); also elsewhere on the board

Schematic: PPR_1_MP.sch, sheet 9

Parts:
C_IMU_B_1: .1uF; 0402-CAP
C_IMU_CP_1: 2.2nF; 0402-CAP
C_IMU_FILT_1: .1uF; 0402-CAP
I2C_PULLUP_1, I2C_PULLUP_2: 10k; R0402
U5: TESTING_MPU-6050-1; TESTING_QFN-24-4MM2
VLOGIC_BYPASS_1: 10nF; 0402-CAP

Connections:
+3V3: C_IMU_B_1.2, I2C_PULLUP_1.2, I2C_PULLUP_2.2, U5.8 (VLOGIC), U5.13 (VDD), VLOGIC_BYPASS_1.2; also elsewhere on the board
CPOUT_1: C_IMU_CP_1.2, U5.20 (CPOUT)
GND: C_IMU_B_1.1, C_IMU_CP_1.1, C_IMU_FILT_1.1, U5.1 (CLKIN), U5.9 (AD0), U5.11 (FSYNC), U5.18 (GND), VLOGIC_BYPASS_1.1; also elsewhere on the board
IMU_IRQ_1: U5.12 (INT)
IMU_SCL_1: I2C_PULLUP_1.1, U5.23 (SCL); also elsewhere on the board
IMU_SDA_1: I2C_PULLUP_2.1, U5.24 (SDA); also elsewhere on the board
REGOUT_1: C_IMU_FILT_1.2, U5.10 (REGOUT)

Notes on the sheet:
I2C ADDR Select

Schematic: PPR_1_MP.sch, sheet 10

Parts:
C_IMU_DC_1: .1uF; 0402-CAP
U$12: MS5611-01BA

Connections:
+3V3: C_IMU_DC_1.2, U$12.1 (VDD), U$12.2 (PS); also elsewhere on the board
GND: C_IMU_DC_1.1, U$12.3 (GND), U$12.4 (CSB1), U$12.5 (CSB2); also elsewhere on the board
IMU_SCL_1: U$12.8 (SCLK); also elsewhere on the board
IMU_SDA_1: U$12.7 (SDI/SDA); also elsewhere on the board

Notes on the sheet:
Connect PS_SDA_x to microcontroller SDA pin
Connect PS_SCL_x to microcontroller SCL pin

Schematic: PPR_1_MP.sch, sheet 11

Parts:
JP10: PINHD-1X2; 1X02

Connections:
GND: JP10.2; also elsewhere on the board
V+: JP10.1; also elsewhere on the board


Board: 2 copper layers, 41.5 x 38.5 mm, 62 parts (0 on the bottom side), 51 nets.

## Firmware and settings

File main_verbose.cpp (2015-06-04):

/*
2015.6.3
Smores mother board main code
Location: Embedded/ecosystem/projects/smores_stm32



Overview:
This code is for uploading to the STM32F303XC in the motherboard of SMORES

(---what this code mainly do---)


receive command and execute
generate trajectories
PID control 
position control
torque control
speed control


Questions: 


using so much flag maybe not a good idea for readability(especially they are not commented)?? Is there other way?
Can the declaration of variables put outside as a file?
Can the different part be seperated into different files so that the main.cpp will not be so long. So that it can show the high level construction of this code 









*/




#include "common_peripherals.h"   // where ? 
#include "system_clock.h"         // ?? 
#include "mBus.h"             // TWX: location: ecosystem/stm32/c/user/inc

// common components 
#include "common_message_types.h"   // TWX: location: ecosystem/common/c/user/inc
// common messages
#include "usb_interface.h"    // TWX: location: ecosystem/common/cpp/user/inc
// usb interface
//#include "mBus.h"

// common libraries
#include "project_message_types.h"  // ??
#include "error_reporting.h"
#include <string.h> 
//needed for memset
//#define   mBUS 1

// user libraries
#include "Wheel_Control.h"   // TWX: ecosystem/smores_common/cpp/inc 
#include "Trajectory.h"      // TWX: ecosystem/smores_common/cpp/inc 

//#define TELECONTROL
//#define POSITION_CONTROL
//#define SPEED_CONTROL


//TWX: what's this for (in which part it was used)
// face ping request messages:
#define LEFT_FACE_PING   121
#define RIGHT_FACE_PING  122
#define TOP_FACE_PING    123
#define BOTTOM_FACE_PING 124

//TWX: what's this for (in which part it was used)
/*   face macros:   */
#define LEFT_FACE 21  // left
#define RIGHT_FACE 22  // right
#define TOP_FACE 23  // top
#define BOTTOM_FACE 24  // bottom

//TWX: address in I2C communication
/*   face i2c address macros:  */
#define BOTTOM_FACE_I2C_ADDRESS 0x0B
#define LEFT_FACE_I2C_ADDRESS   0x0A
#define RIGHT_FACE_I2C_ADDRESS  0x0C
#define TOP_FACE_I2C_ADDRESS    0x0D

//TWX: what's this for (in which part it was used)
/*   face board macros:   */
#define MAGNETS_ON  0xA2
#define MAGNETS_OFF 0xA3
#define FACE_PING   0xA5

//TWX: what's this for (in which part it was used)
// feecback cmd
#define GET_STATES 0xA4

#define UPDATE_GOAL 10
#define SEND_DATA   20


//TWX: these declaration of variables needs to be reorganized(which belongs to which part) and put outside

float path_left[501];
float velocity_left[501];    // max is 100s

float path_speed_left[165];
float velocity_speed_left;    // max is 40000


PID_State left_wheel_stateGoal; //TWX: Class definition in ecosystem/smores_common/cpp/inc/PID_control.h . this is for setting goal position and speed of a wheel
bool init_flag_left;
bool global_flag_left;
bool start_flag_left;
int timer_counter_left;
int update_times_left;
int16_t counter_left;
int16_t index_position_left;
bool start_control_flag_left;


bool global_flag_speed_left;
int timer_counter_speed_left;
int update_times_speed_left;
int16_t counter_speed_left;
int16_t index_speed_left;
bool start_control_speed_flag_left;

float path_right[501];
float velocity_right[501];    // min duration is 1.5

float path_speed_right[165];
float velocity_speed_right;    // max is 40000

PID_State right_wheel_stateGoal;
bool init_flag_right;
bool global_flag_right;
bool start_flag_right;
int timer_counter_right;
int update_times_right;
int16_t counter_right;
int16_t index_position_right;
bool start_control_flag_right;


bool global_flag_speed_right;
int timer_counter_speed_right;
int update_times_speed_right;
int16_t counter_speed_right;
int16_t index_speed_right;
bool start_control_speed_flag_right;

float path_pan[501];
float velocity_pan[501];    // min duration is 1.5

float path_speed_pan[165];
float velocity_speed_pan;    // max is 40000

PID_State pan_wheel_stateGoal;
bool init_flag_pan;
bool global_flag_pan;
bool start_flag_pan;
int timer_counter_pan;
int update_times_pan;
int16_t counter_pan;
int16_t index_position_pan;
bool start_control_flag_pan;


bool global_flag_speed_pan;
int timer_counter_speed_pan;
int update_times_speed_pan;
int16_t counter_speed_pan;
int16_t index_speed_pan;
bool start_control_speed_flag_pan;

float path_tilt[501];
float velocity_tilt[501];    // min duration is 1.5

PID_State tilt_wheel_stateGoal;
bool init_flag_tilt;
bool global_flag_tilt;
bool start_flag_tilt;
int timer_counter_tilt;
int update_times_tilt;
int16_t counter_tilt;
int16_t index_position_tilt;
bool start_control_flag_tilt;

bool pan_ready_flag;
bool tilt_ready_flag;

uint16_t handleFacePing(uint16_t cmd) {
/*  Handles a face name request by asking the face to return its name, and then 
    sending that information back to matlab over USB.
*/
    // Send a ping to a face, and receive data back:
    // Note: A left-shift of 1 (<< 1) appends a zero in the least significant bit
    //       of the address.  This indicates I2C read (as opposed to write).
    uint8_t data = 0xff;
    switch(cmd) {
    case LEFT_FACE_PING:
        //mBusReadBurst(0b01, FACE_PING, 1, &data, 1);
        data = mBusRead(LEFT_FACE_I2C_ADDRESS<<1, FACE_PING, 1);   // TWX: what <<1 means here?
        break;
    case RIGHT_FACE_PING:
        data = mBusRead(RIGHT_FACE_I2C_ADDRESS<<1, FACE_PING, 1);
        break;
    case TOP_FACE_PING:
        data = mBusRead(TOP_FACE_I2C_ADDRESS<<1, FACE_PING, 1);
        break;
    case BOTTOM_FACE_PING:
        data = mBusRead(BOTTOM_FACE_I2C_ADDRESS<<1, FACE_PING, 1);
        break;
    }
    return (uint16_t)data;
    // Send the face response back to Matlab:
    //MsgModule tx_msg;
    //tx_msg.data = (uint16_t)data;  //tx_msg.data is a uint16
    //usb.SendPacket(MsgModuleType, (uint8_t*)&tx_msg, sizeof(tx_msg));
    //mBlueTOGGLE;
}

int main (void){
    InitPeripherals();
    
    UsbInterface usb = UsbInterface();
    usb.Init();

    //XJ: magnet on-off command;
     
    char slave_cmd;

    // power on flag
    bool power_on_flag = 1;
    bool counter_left_power_on = 1;
    bool counter_right_power_on = 1;
    bool counter_pan_power_on = 1;
    bool counter_tilt_power_on = 1;
    
    
    // torque control flag
    bool torque_flag_left = 0;
    bool torque_flag_right = 0;
    bool torque_flag_pan_tilt = 0;
    
    // feedback control init part
    Motor left_wheel_motor;     //TWX: class definition in ecosystem/smores_common/cpp/inc/DC_Motor.h 
    Motor right_wheel_motor;
    Motor right_pan_tilt_motor;
    Motor left_pan_tilt_motor;

    //XJ: right inner motor init
    //TWX: definition in ecosystem/smores_common/cpp/inc/DC_Motor.h 
    right_pan_tilt_motor.GPIO_Direction_GPIOx = GPIOB;
    right_pan_tilt_motor.GPIO_Direction_Pin = GPIO_Pin_2;
    right_pan_tilt_motor.GPIO_Direction_RCC = RCC_AHBPeriph_GPIOB;
    right_pan_tilt_motor.GPIO_PWM_GPIOx = GPIOA;
    right_pan_tilt_motor.GPIO_PWM_Pin = GPIO_Pin_8;
    right_pan_tilt_motor.GPIO_PWM_PinSource = GPIO_PinSource8;
    right_pan_tilt_motor.GPIO_PWM_AF = GPIO_AF_6;
    right_pan_tilt_motor.GPIO_PWM_RCC = RCC_AHBPeriph_GPIOA;
    right_pan_tilt_motor.TIMx = TIM1;
    right_pan_tilt_motor.TIMx_Channel = TIM_Channel_1;
    right_pan_tilt_motor.TIMx_RCC = RCC_APB2Periph_TIM1;
    right_pan_tilt_motor.TIMx_Mode = TIM_OCMode_PWM1;
    right_pan_tilt_motor.direction = Bit_RESET;
    right_pan_tilt_motor.speed = 0;
    Motor_Init(right_pan_tilt_motor);
    
    //XJ: left inner motor init
   
    left_pan_tilt_motor.GPIO_Direction_GPIOx = GPIOB;
    left_pan_tilt_motor.GPIO_Direction_Pin = GPIO_Pin_15;
    left_pan_tilt_motor.GPIO_Direction_RCC = RCC_AHBPeriph_GPIOB;
    left_pan_tilt_motor.GPIO_PWM_GPIOx = GPIOB;
    left_pan_tilt_motor.GPIO_PWM_Pin = GPIO_Pin_14;
    left_pan_tilt_motor.GPIO_PWM_PinSource = GPIO_PinSource14;
    left_pan_tilt_motor.GPIO_PWM_AF = GPIO_AF_1;
    left_pan_tilt_motor.GPIO_PWM_RCC = RCC_AHBPeriph_GPIOB;
    left_pan_tilt_motor.TIMx = TIM15;
    left_pan_tilt_motor.TIMx_Channel = TIM_Channel_1;
    left_pan_tilt_motor.TIMx_RCC = RCC_APB2Periph_TIM15;
    left_pan_tilt_motor.TIMx_Mode = TIM_OCMode_PWM1;
    left_pan_tilt_motor.direction = Bit_RESET;
    left_pan_tilt_motor.speed = 0;
    Motor_Init(left_pan_tilt_motor);

    //XJ: right face motor init
    
    right_wheel_motor.GPIO_Direction_GPIOx = GPIOA;
    right_wheel_motor.GPIO_Direction_Pin = GPIO_Pin_10;
    right_wheel_motor.GPIO_Direction_RCC = RCC_AHBPeriph_GPIOA;
    right_wheel_motor.GPIO_PWM_GPIOx = GPIOA;
    right_wheel_motor.GPIO_PWM_Pin = GPIO_Pin_9;
    right_wheel_motor.GPIO_PWM_PinSource = GPIO_PinSource9;
    right_wheel_motor.GPIO_PWM_AF = GPIO_AF_6;
    right_wheel_motor.GPIO_PWM_RCC = RCC_AHBPeriph_GPIOA;
    right_wheel_motor.TIMx = TIM1;
    right_wheel_motor.TIMx_Channel = TIM_Channel_2;
    right_wheel_motor.TIMx_RCC = RCC_APB2Periph_TIM1;
    right_wheel_motor.TIMx_Mode = TIM_OCMode_PWM1;
    right_wheel_motor.direction = Bit_RESET;
    right_wheel_motor.speed = 0;
    Motor_Init(right_wheel_motor);

    //XJ: left face motor init
    
    left_wheel_motor.GPIO_Direction_GPIOx = GPIOA;
    left_wheel_motor.GPIO_Direction_Pin = GPIO_Pin_0;
    left_wheel_motor.GPIO_Direction_RCC = RCC_AHBPeriph_GPIOA;
    left_wheel_motor.GPIO_PWM_GPIOx = GPIOA;
    left_wheel_motor.GPIO_PWM_Pin = GPIO_Pin_1;
    left_wheel_motor.GPIO_PWM_PinSource = GPIO_PinSource1;
    left_wheel_motor.GPIO_PWM_AF = GPIO_AF_1;
    left_wheel_motor.GPIO_PWM_RCC = RCC_AHBPeriph_GPIOA;
    left_wheel_motor.TIMx = TIM2;
    left_wheel_motor.TIMx_Channel = TIM_Channel_2;
    left_wheel_motor.TIMx_RCC = RCC_APB1Periph_TIM2;
    left_wheel_motor.TIMx_Mode = TIM_OCMode_PWM1;
    left_wheel_motor.direction = Bit_RESET;
    left_wheel_motor.speed = 0;
    Motor_Init(left_wheel_motor);

    //XJ: motor min-max speed
    int8_t motor_cmd_min = -50;
    uint8_t motor_cmd_max = 50;

    //XJ: motor min-max position
    float min_pos = -32767;
    float max_pos = 32767;

    //XJ: left face motor PID control
    //TWX: PID controller definition in ecosystem/projects/smores_pid_control/stm32f303xc/inc/PID_Control.h

    float Kp = 0.018, Ki = 0, Kd = 0.0002;
    PID_Controller left_wheel_pid_controller(Kp, Ki, Kd, motor_cmd_min, motor_cmd_max);
    Wheel_Controller_OneMotor left_wheel_control(&left_wheel_pid_controller, left_wheel_motor);

    //XJ quintic trajectory init
    //TWX: Polynomial class definition Embedded/ecosystem/smores_common/cpp/inc/Polynomial.h
    float coeff_left[6] = {0,0,0,0,0,0};
    float duration_left = 0;
    Polynomial p_left(coeff_left, 6);
    float startTime_left = 0;
    float endTime_left = 0;
    uint16_t sectionNum_left = 500;
    Trajectory trajectory_left(startTime_left, endTime_left, sectionNum_left, &p_left);

    //XJ: quintic trajectory velocity init
    float coeff_speed_left[2] = {0,0};
    Polynomial p_speed_left(coeff_speed_left, 2);
    uint16_t positionNum_left = 164;
    Trajectory trajectory_speed_left(positionNum_left, min_pos, max_pos, &p_speed_left);
    trajectory_speed_left.GeneratePositionVelocityTrajectory(path_speed_left, &velocity_speed_left);
    update_times_speed_left = positionNum_left;
    
    //XJ: goal position velocity init
    left_wheel_stateGoal.Position = 0;
    left_wheel_stateGoal.Speed = 0;
    left_wheel_control.setStateGoal(left_wheel_stateGoal);

    PID_State left_wheel_currentState;

    char slave_addr_left = 0x14;
    uint8_t data_left[7] = {0,0,0,0,0,0,0};

    int16_t current_position_left = 0;
    int32_t current_velocity_left = 0;
    int8_t left_wheel_cmd = 0;

    //XJ: right face motor PID control
    PID_Controller right_wheel_pid_controller(Kp, Ki, Kd, motor_cmd_min, motor_cmd_max);
    Wheel_Controller_OneMotor right_wheel_control(&right_wheel_pid_controller, right_wheel_motor);

    //XJ: quintic trajectory init
    float coeff_right[6] = {0,0,0,0,0,0};
    float duration_right = 0;
    Polynomial p_right(coeff_right, 6);
    float startTime_right = 0;
    float endTime_right = 0;
    uint16_t sectionNum_right = 500;
    Trajectory trajectory_right(startTime_right, endTime_right, sectionNum_right, &p_right);

    //XJ: quintic trajectory velocity init
    float coeff_speed_right[2] = {0,0};
    Polynomial p_speed_right(coeff_speed_right, 2);
    uint16_t positionNum_right = 164;
    Trajectory trajectory_speed_right(positionNum_right, min_pos, max_pos, &p_speed_right);
    trajectory_speed_right.GeneratePositionVelocityTrajectory(path_speed_right, &velocity_speed_right);
    update_times_speed_right = positionNum_right;
    
    //XJ: goal position velocity init
    right_wheel_stateGoal.Position = 0;
    right_wheel_stateGoal.Speed = 0;
    right_wheel_control.setStateGoal(right_wheel_stateGoal);


    PID_State right_wheel_currentState;

    char slave_addr_right = 0x18;
    uint8_t data_right[7] = {0,0,0,0,0,0,0};


    int16_t current_position_right = 0;
    int32_t current_velocity_right = 0;
    int8_t right_wheel_cmd = 0;





    // pan and tilt DoF control
    float Kd_pan = 0.00011;
    float Kd_tilt = 0.00011;
    PID_Controller wheel_pid_controller_pan(Kp, Ki, Kd_pan, motor_cmd_min, motor_cmd_max);
    PID_Controller wheel_pid_controller_tilt(Kp, Ki, Kd_tilt, motor_cmd_min, motor_cmd_max);
    Wheel_Controller_Pan_Tilt wheel_control_pan_tilt(&wheel_pid_controller_pan, &wheel_pid_controller_tilt, left_pan_tilt_motor, right_pan_tilt_motor);

    //XJ: pan quintic trajectory init
    float coeff_pan[6] = {0,0,0,0,0,0};
    float duration_pan = 0;
    Polynomial p_pan(coeff_pan, 6);
    float startTime_pan = 0;
    float endTime_pan = 0;
    uint16_t sectionNum_pan = 500;
    Trajectory trajectory_pan(startTime_pan, endTime_pan, sectionNum_pan, &p_pan);

    //XJ: pan quintic trajecoty velocity init
    float coeff_speed_pan[2] = {0,0};
    Polynomial p_speed_pan(coeff_speed_pan, 2);
    uint16_t positionNum_pan = 164;
    Trajectory trajectory_speed_pan(positionNum_pan, min_pos, max_pos, &p_speed_pan);
    trajectory_speed_pan.GeneratePositionVelocityTrajectory(path_speed_pan, &velocity_speed_pan);
    update_times_speed_pan = positionNum_pan;  //TWX:  ??
    
    //XJ: goal position velocity init
    pan_wheel_stateGoal.Position = 0;
    pan_wheel_stateGoal.Speed = 0;

    PID_State pan_wheel_currentState;

    char slave_addr_pan = 0x1A;
    uint8_t data_pan[7] = {0,0,0,0,0,0,0};

    int16_t current_position_pan = 0;
    int32_t current_velocity_pan = 0;
    int8_t left_motor_cmd = 0;
    int8_t right_motor_cmd = 0;

    // tilt DoF control
    float coeff_tilt[6] = {0,0,0,0,0,0};
    float duration_tilt = 0;
    Polynomial p_tilt(coeff_tilt, 6);
    float startTime_tilt = 0;
    float endTime_tilt = 0;
    uint16_t sectionNum_tilt = 500;
    Trajectory trajectory_tilt(startTime_tilt, endTime_tilt, sectionNum_tilt, &p_tilt);
    
    tilt_wheel_stateGoal.Position = 0;
    tilt_wheel_stateGoal.Speed = 0;

    wheel_control_pan_tilt.setStateGoal(pan_wheel_stateGoal, tilt_wheel_stateGoal);

    PID_State tilt_wheel_currentState;

    char slave_addr_tilt = 0x16;
    uint8_t data_tilt[7] = {0,0,0,0,0,0,0};

    int16_t current_position_tilt = 0;
    int32_t current_velocity_tilt = 0;




    //XJ: turn on the LEDS and turn off them when power on
    mWhiteON;mRedON;mBlueON;mYellowON;
    DelayMilliseconds(1000);
    mWhiteOFF;mRedOFF;mBlueOFF;mYellowOFF;

    //XJ: flag init
    start_flag_left = 0;
    start_flag_right = 0;
    start_flag_pan = 0;
    start_flag_tilt = 0;
    pan_ready_flag = 0;
    tilt_ready_flag = 0;
    char cmd;
    PlayTimebase();  //TWX: what is playtimebase??
    // feedback control part end //

    //XJ
    /**
    main loop. 
    Do the most part of the work
    Read the command and do the command
    **/
    while(1)
    {
//        mGreenTOGGLE;

        uint8_t *rx_data;
        uint8_t rx_length;
        uint8_t is_data = 0;

        //XJ: read the command from USB
        //TWX: to rx_data, the cmd type is defined by rx_data[0], which could be MsgCmdType MsgMagnetType MsgControlType MsgTrajectoryPositionType  MsgTrajectoryVelocityType MsgTorqueType indicating type of the message received
        usb.GetBytes();
        while(usb.PeekPacket(&rx_data, &rx_length)) {
            uint8_t type = rx_data[0];

            //XJ: send data to the buffer?
            //TWX: what is MsgCmdType? and where can we find it
            if(type == MsgCmdType) {
                mGreenTOGGLE;
                MsgCmd *rx_msg = ((MsgCmd*) (rx_data+1));
                if(rx_msg->cmd > 100) {
                    mYellowTOGGLE;
                    MsgModule tx_msg;
                    tx_msg.data = handleFacePing(rx_msg->cmd);
                    usb.SendPacket(MsgModuleType, (uint8_t*)&tx_msg, sizeof(tx_msg));
                    is_data = 1;
                }
            }

            //XJ: choose a face and set the magnet on or off
            else if (type == MsgMagnetType) {
                MsgMagnet *rx_msg = ((MsgMagnet*) (rx_data+1)); 
                switch (rx_msg->face) {
                case LEFT_FACE:
//                    mWhiteTOGGLE;
                    if (rx_msg->state)
                    {
                        slave_cmd = MAGNETS_ON;
                    }
                    else
                    {
                        slave_cmd = MAGNETS_OFF;
                    }
                    mBusWriteNoAdd(LEFT_FACE_I2C_ADDRESS << 1, slave_cmd, 1);
                    break;
                case RIGHT_FACE:
//                    mGreenTOGGLE;
                    if (rx_msg->state)
                    {
                        slave_cmd = MAGNETS_ON;
                    }
                    else
                    {
                        slave_cmd = MAGNETS_OFF;
                    }
                    mBusWriteNoAdd(RIGHT_FACE_I2C_ADDRESS << 1, slave_cmd, 1);
                    break;
                case TOP_FACE:
//                    mRedTOGGLE;
                    if (rx_msg->state)
                    {
                        slave_cmd = MAGNETS_ON;
                    }
                    else
                    {
                        slave_cmd = MAGNETS_OFF;
                    }
                    mBusWriteNoAdd(TOP_FACE_I2C_ADDRESS << 1, slave_cmd, 1);
                    break;
                case BOTTOM_FACE:
//                    mBlueTOGGLE;
                    if (rx_msg->state)
                    {
                        slave_cmd = MAGNETS_ON;
                    }
                    else
                    {
                        slave_cmd = MAGNETS_OFF;
                    }
                    mBusWriteNoAdd(BOTTOM_FACE_I2C_ADDRESS << 1, slave_cmd, 1);
                    break;
                }
            }

            //XJ: control mode
            // TWX: reads msgfrom
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

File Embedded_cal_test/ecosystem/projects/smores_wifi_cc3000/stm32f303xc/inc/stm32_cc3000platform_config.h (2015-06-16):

/**
  ******************************************************************************
  * @file    stm32_cc3000platform_config.h 
  * @author  
  * @version V1.1.0
  * @date    06-June-2014
  * @brief   Header for stm32_cc3000.c module
  ******************************************************************************
*/
 
/* Define to prevent recursive inclusion -------------------------------------*/
#ifndef PLATFORM_CONFIG_H
#define	PLATFORM_CONFIG_H

#include "stm32f30x_syscfg.h"

#ifdef	__cplusplus
extern "C" {
#endif


/* Define the external interrupt interface with CC3000 */
#define CC3000_IRQ_RCC         RCC_AHBPeriph_GPIOA
#define CC3000_IRQ_PORT        GPIOA
#define CC3000_IRQ_PIN         GPIO_Pin_2
#define CC3000_IRQ_EXTI_LINE   EXTI_Line2
#define CC3000_IRQ_EXTI_PORT   EXTI_PortSourceGPIOA
#define CC3000_IRQ_EXTI_PIN    GPIO_PinSource2
#define CC3000_IRQ_EXTI_CH     EXTI2_TS_IRQn

/* Define GPIO pin to interface with the VBEN pin on CC3000*/
#define CC3000_VBAT_EN_RCC     RCC_AHBPeriph_GPIOA
#define CC3000_VBAT_EN_PORT    GPIOA
#define CC3000_VBAT_EN_PIN     GPIO_Pin_3

/* Communication boards SPIx Interface with CC3000*/
#define CC3000_CS_RCC          RCC_AHBPeriph_GPIOA
#define CC3000_CS_PORT         GPIOA
#define CC3000_CS_PIN          GPIO_Pin_4

#define CC3000_SCK_GPIO_PORT   GPIOA
#define CC3000_SCK_GPIO_SOURCE GPIO_PinSource5
#define CC3000_SCK_AF   	   GPIO_AF_5
#define CC3000_SCK_GPIO_PIN    GPIO_Pin_5

#define CC3000_MISO_GPIO_PORT   GPIOA
#define CC3000_MISO_GPIO_SOURCE GPIO_PinSource6
#define CC3000_MISO_AF   	    GPIO_AF_5
#define CC3000_MISO_GPIO_PIN    GPIO_Pin_6

#define CC3000_MOSI_GPIO_PORT   GPIOA
#define CC3000_MOSI_GPIO_SOURCE GPIO_PinSource7
#define CC3000_MOSI_AF   	    GPIO_AF_5
#define CC3000_MOSI_GPIO_PIN    GPIO_Pin_7

#define CC3000_SPI			    SPI1
#define CC3000_SPI_CLK		    RCC_APB2Periph_SPI1

/* Define GPIO configuration of the SPI peripheral*/ 
#define CC3000_SPI_GPIO_MODE	GPIO_Mode_AF
#define CC3000_SPI_GPIO_SPEED	GPIO_Speed_50MHz
#define CC3000_SPI_GPIO_OTYPE	GPIO_OType_PP
#define CC3000_SPI_GPIO_PUPD	GPIO_PuPd_NOPULL

/* Connection properties. Change according to settings*/
//IP and PORT for transmission
#define SEND_PORT_NUM 			 4242
#define SEND_ADDR1 				 0xFF0AA8C0  // 192.168.10.255
#define SEND_ADDR2				 0x640AA8C0  // 192.168.10.100
//IP and PORT for RECEPTION
#define RECV_PORT_NUM 			 8888
#define LISTEN_ADDR  			 0x00 // Receive from all

//AP Information 
#define WLAN_SSID    			  "Gumstix_Smores"
#define WLAN_PASS    			  "Modlab3142"
// Security can be WLAN_SEC_UNSEC, WLAN_SEC_WEP, WLAN_SEC_WPA or WLAN_SEC_WPA2
#define WLAN_SECURITY					  WLAN_SEC_WPA2
#define CC3000_APP_BUFFER_SIZE  	          (5)
#define CC3000_RX_BUFFER_OVERHEAD_SIZE        (20)

//GENERIC ROUTER INFORMATION (change according to router)
#define STATIC_SUBNET_MASK 			 0x00FFFFFF//255.255.255.0
#define STATIC_DEFAULT_GATEWAY 		 0x010AA8C0//192.168.10.1
#define STATIC_DNS_SERVER 			 0x010AA8C0//192.168.10.1
#define MOD_START_IP				 0x6E0AA8C0 //Module IPs will start from 
                                          //192.168.10.(110+module number)



#ifdef	__cplusplus
}
#endif

#endif	/* PLATFORM_CONFIG_H */

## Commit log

2015-06-16 atmega cali test
    [BOM.ods, Battery_Coin-Cell_CR2032_Horizontal.sch, Battery_Li-Po_2000mAh.sch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]
2015-06-17 motor works
2015-07-20 fully functionalized auto calibration except wiper_encoder.h part

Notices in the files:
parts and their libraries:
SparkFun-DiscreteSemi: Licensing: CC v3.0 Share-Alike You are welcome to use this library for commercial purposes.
